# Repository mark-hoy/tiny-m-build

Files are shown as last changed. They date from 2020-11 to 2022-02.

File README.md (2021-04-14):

# tiny-m-build
- [tiny-m-build](#tiny-m-build)
  * [WORK IN PROGRESS](#work-in-progress)
  * [Power](#power)
  * [My BOM](#my-bom)
  * [Build Platform + Plate Information](#build-platform---plate-information)
  * [Stepper Motor Light Reading](#stepper-motor-light-reading)
  * [Frame Assembly](#frame-assembly)
  * [Top](#top)
  * [Hinged TopHat](#hinged-tophat)
- [Electronics](#Electronics)
- [Software](#software)
  * [Raspberry Pi Setup](#raspberry-pi-setup)
  * [Fluidd Pi](#fluidd-pi)
  * [Fluidd](#fluidd)
  * [Mainsail OS](#mainsail-os)
  * [Klipper onto SKR Mini E3 V2](#klipper-onto-skr-mini-e3-v2)
    * [Flashing MCU](#Flashing MCU)
    * [Klipper Configuration](#Klipper Configuration)
  * [Wiring](#wiring)
  
### Klipper Configuration
  
- [Assembly](#assembly)
  * [Rails](#rails)
  * [Rails and Build Plate](#rails-and-build-plate)
- [Extruder](#extruder)
  * [Sherpa Mini](#sherpa-mini)

<small><i><a href='http://ecotrust-canada.github.io/markdown-toc/'>Table of contents generated with markdown-toc</a></i></small>

## WORK IN PROGRESS
This is my particular spin on the Tiny-M build, a variant of the Voron V0 using Mitsumi 2020 Extrusions and Nema 17 motors.  The Voron machines are home build high performance printers. With the V0 being the smallest of the series. The numbering scheme, V0, V1, V2 represent different machines, so don't get confused that's it's a revision.

My version of this is slightly different than the online CAD image. I want to used a BTT SKR mini E3 V2, a 24v heated bed (instead of 120v ac) and a direct drive sherpa mini instead of the regular boden drive.

see the cad image at 
https://github.com/gsl12/Tiny-M

I've finished the build. Will probably go with a simpler enclosure rather than the folding top hat, but need to design it still.
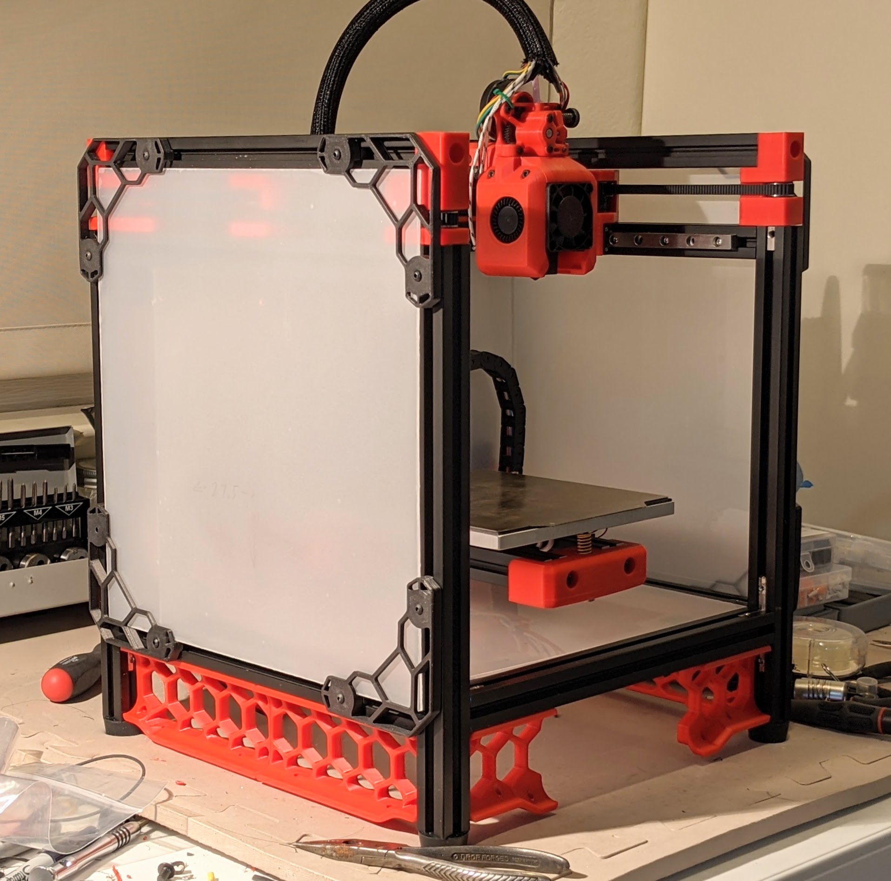
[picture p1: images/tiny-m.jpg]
tiny-m image


Many more build pictures at https://photos.app.goo.gl/qUpFSqQ5FszeDbXW6

The first things I'll link are the Voron V0 build and the Tiny-M repo.
I'd like to use a small direct hot end instead of the standard Voron V0 Boden so that it will easily print flexable material.
In addition, I really like the two position hinged TopHat by hartk1213

There is a very active Discord channel for VoronDesign. The users are really helpful and friendly which for a home build
3d printer is a huge win.

Voron V0 - https://vorondesign.com/voron0

Tiny-M https://github.com/gsl12/Tiny-M

Sherpa Mini-Extruder https://github.com/Annex-Engineering/Sherpa_Mini-Extruder

Hinged Top Hat - https://github.com/gsl12/Tiny-M/tree/master/STLs/usermods/2020_Hinged_TopHat_Print

Motion controller - BIGTREETECH SKR Mini E3 V2.0 New Upgrade Control Board 32Bit with TMC2209 

Job control - Raspberry Pi Zero W, Pi 3 or 4?

T8x4 ptfe coated Lead Screw + POM - 215mm	 *Note: will have to cut to length as this isn't standard.

Many images so far from Xile on Voron group on discord

## Power
Want to use an external 24v supply and then all 24v on the Tiny-M. This means a 24v heated bed which is normally 120v ac. It removed all 120ac from the underside of the build making it a bit safer. Sourcing the bed heater is harder though as is the connection of the power to the chassis.

Got the DC power using the following.

External Mean Well 220 watt 24v DC power supply https://www.digikey.com/en/products/detail/GST220A24-R7B/1866-2085-ND/7703643?itemSeq=348860603 \
Power inlet to match - https://www.digikey.com/en/products/detail/KPJX-PM-4S/2092-KPJX-PM-4S-ND/9990081?itemSeq=348766398 \
Power switch - https://www.digikey.com/en/products/detail/RB141C1000-135/EG5684-ND/8540808?itemSeq=348859736 \
NOTE: The power switch burned it's light out at 24v, suggest adding a voltage drop resistor.

While I really like the idea of 24v of external power with a distribution via this nifty board, I didn't want to have to manufacture a 4 layer board just for my power input, so I decided to go with the simpler solution above....
https://github.com/JNP-1/VoronUsers/tree/master/printer_mods/JNP/PCBs/Supply_PCB

BOM https://github.com/JNP-1/VoronUsers/blob/master/printer_mods/JNP/PCBs/Supply_PCB/BOM/BOM_Supply_PCB_V1.0.txt

Along with an external power brick with a microfit connection\
https://www.digikey.com/en/products/detail/VES220PS24/1470-VES220PS24-ND/10440644?itemSeq=347136397

Use the following when determining how much power a guage of wire can handle https://www.engineeringtoolbox.com/wire-gauges-d_419.html

## My BOM
https://docs.google.com/spreadsheets/d/1UV62ADl2gtK5vL0fV1nwevR6O9Ppzs0MBe7jnsI-jo4/edit?usp=sharing

## Build Platform + Plate Information
The build plate should be either ATP-5 or MIC6 Cast Aluminum 6" x 6" x 1/4" which is about 150mm x 150mm x 6mm onto which a magnetic layer is added, topped with a spring steel build plate.

The heater for the bed should be aprox 0.4 watts/cm^2.  So 15cm x 15cm = 255cm^2    255 * 0.4 = 102 watts. Less power will heat slower, more might be ok, but don't go crazy.  See the following for great info https://duet3d.dozuki.com/Wiki/Choosing_a_bed_heater

## Stepper Motor Light Reading
Many Nema 17 will fit into the space. 
https://duet3d.dozuki.com/Wiki/Choosing_and_connecting_stepper_motors

## Frame Assembly
Depending on if you are drilling + tapping for your rails or using the 90 degree internal connectors (or possibly both!)

If you are drilling (and have a printer) you can make a guide:
See the STL drill template for the holes: 10, 36 and 60

The bottom extrusions have 50mm of space to the bottom of the uprights.
The back is 26mm on the side beams for a total of 26mm + 20mm total (from the back beam).

## Top
While I really like the way the hinged TopHat works, I think I'll go with taller side panels, a taller door panel and a fixed top. I haven't had to have access to the top since I built it. I will re-use the hinged top-hat basic sizes though as the connection into the rails via the M5 is solid.

## Hinged TopHat
The hinged top hat has two positions it can stay in. There is a 2020 TopHat for V0 that I've patterned the following on
(was at https://github.com/gsl12/Tiny-M/tree/master/STLs/usermods/2020_Hinged_TopHat_Print)

**The following measurements have not been verified in an actual build.**\
Verticals\
Back 2 x 75 mm\
Front 2 x 92 mm

Horizontal\
Front 2 x 260 mm\
Back 1 x 260 mm, 1 x 274 mm

Sides\
Top Right/Left 2 x 260 mm\
Bottom Right/Left 2 x 230 mm

Totals\
2 x 75 mm\
2 x 92 mm\
2 x 230 mm\
5 x 260 mm\
1 x 274 mm

# Electronics

The BTT SRK mini E3 V2 (not the older models) is my choice for this build. In pariticular, it has a beefier Mosfet for driving the heater bed. It has many other fine updates too: 2 fan outputs. a proper ground return for drivers, and better thermistor circuitry (thanks Ocho).

Raspberry Pi 3/4, or Zero W.  Any of these will work with Klipper software as it's got a fairly light overhead.

Display - FYSETC V2.1 Mini 12864 is what I have on hand. The wiring to the SRK mini E3 V2 is a bit weird. There is a board that plugs into the USB on the Pi that then easily connects to the two 10 pin connectors. Alternatives are possible here.

For the steppers, I chose all LDO motors which have a great reputation. The X/Y/Z are all 0.9 degree LDO 17HS19-2004S (which also deviates from the original Tiny-M BOM with 1.8 degree steppers).

Endstops - I am using some D2FC-F-7N that I had on hand from fixing a Logitech trackball mouse. (I have to ream out the mounting hole to fit M2). 

I would like to try sensorless homing since the TMC2209 support this mode but have not gotten to this yet.

Additional, stealth chop makes the motors REALLY quiet, this would be pretty cool to also try.

# Software

Thinking of using Raspberry Pi 2 (or 3) with Fluidd and Klipper on BTT SKR Mini E3 V2
By using Fluidd Pi, install should be relatively easy. 

The Raspberry Pi runs Klipper which spits out G-code for the Mini E3 to drive the stepper motors.
The Raspberry Pi connects to the Mini E3 via the USB cable that comes with the Mini E3.

## Raspberry Pi Setup

While I'm using a Pi 4, I'll be trying out FluiddPi, so this is just to get the rest of you going should you want to do it all yourself and download an Image. I strongly suggest you go the FluiddPi route....

Download the latest Raspberry Pi OS Lite image, mine was a 5.4 from Dec 2, 2020 and use Etcher or something similar to burn an SD card with the image. I happened to use a 32G card on a Raspberry Pi 4, but smaller cards and slower Pi will also work.

https://www.raspberrypi.org/software/operating-systems/ \
https://github.com/vladbabii/raspberry_os_buster_read_only_fs

## Fluidd Pi
FluiddPi - A Pi image with Klipper, Moonraker, Fluidd and Web Camera support pre-installed. - cadriel/FluiddPI
https://github.com/cadriel/FluiddPI

1. Download the latest FluiddPi Image, I used v1.2.2 at https://github.com/cadriel/FluiddPI/releases/download/v1.2.2/fluiddpi-rpi-lite-v1.2.2.zip
2. Flash your SD card with the image (fluiddpi-rpi-lite-v1.2.2.zip in my case), I used BalenaEtcher for OSX.
3. Connect the Pi to your monitor (funky adapter cable needed for HDMI on Pi 4) and keyboard, login: pi  password: raspberry
4. Run "sudo raspi-config" and walk through each menu item. \
4a. I choose wireless options and connected to my home wireless, but you could also go wired via Ethernet.\
4b. Give your Pi a hostname and probably set it to your timezone for ease of looking at your log files.\
4c. Enable SSH so that you can remotely get into your Pi\
4d. Update Pi with various patches\
4e. exit 'raspi-config' \
4f. update/upgrade the Linux system "sudo apt update" and "sudo apt upgrade"
4e. Reboot and prove all the stuff you just did works

Run "ifconfig" and determine your IP address. Note: You might want to get the MAC address and set a static IP address in your DCHPD configuration of your Wireless Router. Use SSH (on OSX/Linux) or PuTTY on Windows and remotely login to your Pi. The command will be similar to "ssh pi@192.168.1.164" but with your IP address.

In addition, if you browse on your network to http://192.168.1.164/fluidd#/configuration you can start configuration of your system

## Fluidd
https://github.com/cadriel/fluidd/blob/develop/docs/README.md

## Mainsail OS
https://github.com/raymondh2/MainsailOS/releases

How to install \
https://www.youtube.com/watch?v=MK0-MDVJG94

How to configure mainsail \
https://meteyou.github.io/mainsail/setup/

Connecting \
https://discord.com/channels/460117602945990666/741806179247980695/768032201362767893

Web Camera for Mainsail https://lazarofilm.gitbook.io/3d-printing/setting-up-your-pi-camera-for-mainsail

## Klipper onto SKR Mini E3 V2

Klipper code needs to run on the Pi and communicate with the MCU. Our MCU is the BTT SKR Mini E3 V2 and the following is how to set it up.

Note pin difference from earlier SKR mini boards. \

https://github.com/VoronDesign/Voron-0/pull/51 for V2 vs V1.x difference \
https://discord.com/channels/460117602945990666/696930677161197640/746051951447375983 \
https://github.com/VoronDesign/Voron-0/blob/master/VORON-0/Manuals/V0_Setup_Guide.pdf

Another example configuration of SKR Mini E3 V2 for klipper \
https://github.com/KevinOConnor/klipper/blob/master/config/generic-bigtreetech-skr-mini-e3-v2.0.cfg

Copy the appropriate file from the configuration directory in this github to /home/pi/klipper_config/printer.cfg (or similar if you have it in a different place.

Example: OSX & Linux
```console
$ scp configuration/printer.skr.mini.e3.v2.cfg pi@192.168.1.164:/home/pi/klipper_config/printer.cfg
```

Use the following as a reference for configuration of Klipper for BTT SKR mini E3 V2 \
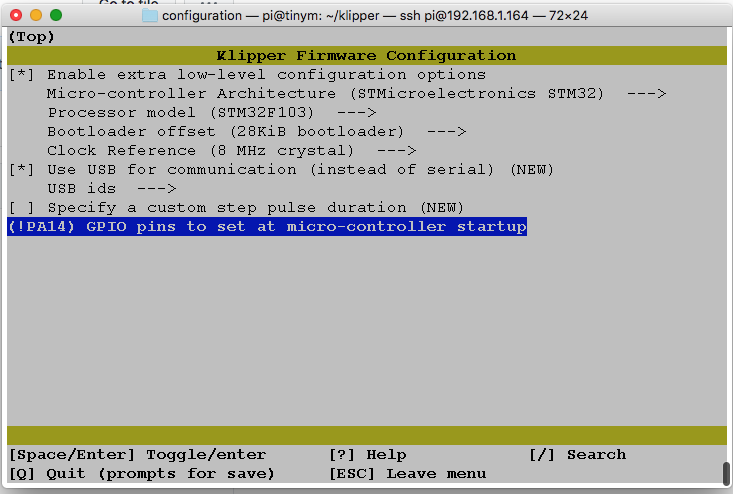
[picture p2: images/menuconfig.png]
cfg image


Then, on the Pi move to the klipper directory
```console
$ cd klipper
$ make menuconfig
. 
. 
. 
~/klipper $ cp out/klipper.bin ~/firmware.bin
```

### Flashing MCU

1. Now remove the SD card from the SKR mini and copy this file onto it.
2. Place card into MCU and apply 24v power, wait 1 minute and turn power off
3. Remove card, and look at the contents and the "firmware.bin" file should have been renamed to "FIRMWARE.CUR" 
4. The MCU is now up to date and ready to work with Klipper

### Klipper Configuration

First power on the Pi and then the SKR Mini E3 V2 then log into the Pi and run a couple of commands

Issue the following command, then plug in the USB cable and you should see something like:

```console
$ dmesg -w -t
...
cdc_acm 1-1.1:1.0: ttyACM0: USB ACM device 
usb 1-1.1: USB disconnect, device number 5 
usb 1-1.1: new full-speed USB device number 6 using xhci_hcd 
usb 1-1.1: New USB device found, idVendor=1d50, idProduct=614e, bcdDevice= 1.00 
usb 1-1.1: New USB device strings: Mfr=1, Product=2, SerialNumber=3 
usb 1-1.1: Product: stm32f103xe 
usb 1-1.1: Manufacturer: Klipper 
usb 1-1.1: SerialNumber: 35FFDB054246313020791057 
cdc_acm 1-1.1:1.0: ttyACM0: USB ACM device
```

Klipper should now be able to use a mapping that contains the serial number, copy this info into the 'serial' line in the configuration file

```console
$ ls /dev/serial/by-id/
usb-Klipper_stm32f103xe_35FFDB054246313020791057-if00
```

Edit the klipper_config file
```console
$ vi klipper_config/printer.cfg 
```

So now the cfg should contain your printer
```console
$ grep serial klipper_config/printer.cfg 
serial: /dev/serial/by-id/usb-Klipper_stm32f103xe_35FFDB054246313020791057-if00
```

If you don't see the /dev/by/serial section, double check your USB cable and ensure each board is correctly powered on.

For Klipper to run without throwing errors, it expects to see valid information from it's configured thermistors. So wire up the hotend thermistor to PA0.

If you don't have a heated bed (or it's not installed yet), then comment out the "[heater_bed]" section as well as the last 5 lines of the printer.cfg file

Remove the last 5 lines in printer.cfg file\
#*# [heater_bed]\
#*# control = pid\
#*# pid_kp = 37.593\
#*# pid_ki = 1.139\
#*# pid_kd = 310.142\

## Wiring Guide
Follow the V0 guide for steppers, limit switches, hot end, bed heater, bed thermal cutoff switch, etc.

The best set of info for this is the V0 assembly manual which is oddly not on the Voron main site, but only in the GitHub location
https://github.com/VoronDesign/Voron-0/blob/master/VORON-0/Manuals/V0_Setup_Guide.pdf

The Wago wire connectors can make your life a bit easier too.

Basic stepper setup
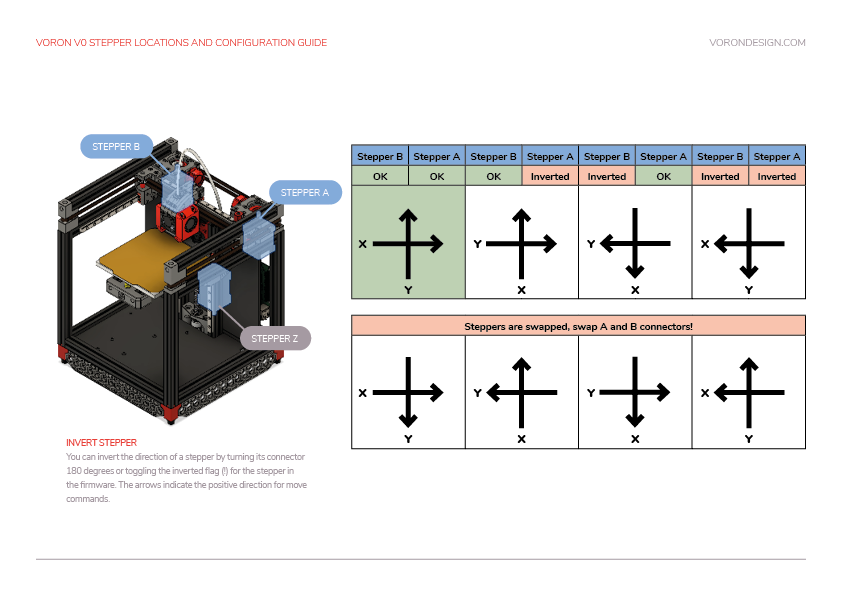
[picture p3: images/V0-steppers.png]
cfg image


Back Left Motor B Connects to X\
Back Right Motor A Connects to Y

Direction of X is inverted as well as Y in the configuration file (at least for my wiring).

# Assembly 

## Rails
Watch the video and note that if you use the 90 degree internal corners, you'll only need two holes in the build plate. You'll still have a bunch of tapping though so worth watching. \
https://www.youtube.com/watch?v=2dvbn0rWA60&feature=youtu.be

## Rails and Build Plate
Carefully review the Tiny-M CAD via OnShape 
https://github.com/gsl12/Tiny-M \
While I found OnShape slow to load on my aging 2011 iMac, it did pretty darn good once loaded.

I believe (but have not verified) that assembly of the tiny-m should be very similar to the V0 rails and build plate, so watch the following video:\
https://youtu.be/Il6koDFPf7w

Build Plate - Wago 221 connectors make for very nice connections on the printer. They are not rated for the temperature at the bed, but unless you are running a very hot enclosed build, they should be OK a distance away. I used a couple of these holders mounted to the rails under the build plate. https://www.thingiverse.com/thing:4579456 The Wago 221 snap into place very firmly.

# Extruder

## Sherpa Mini 
From Anin at https://discord.com/channels/641407187004030997/705183604535459871/785714455178248192

Coffee's video shows the correct assembly order for a K series printer where the lower two screws thread into the toolhead. For a standalone sherpa it might be easier to assemble things in this order:\
1. Install all inserts (including 2 in the rear housing) and bearings, clean up the filament path with a 2mm drill bit\
2. Sand/grind shaft (use the printed tool if necessary)\
3. Insert the 50t gear/shaft assy into the bearing\
4. Stack the core housing on top of the rear housing and install the lower two screws\
5. Install the driven BMG filament gear, add a 5x7x0.5mm waher on top of the gear. Loctite the grub screw\
6. Build and install the idler arm assembly\
7. Install the front housing\
8. Make sure everything runs freely\
9. Install the motor and adjust gear meshing until there is only a tiny bit of backlash\
10. Install the tensioner screw assembly\
Note also that the tensioner screw insert can be up to 6mm long

The video reference.\
https://youtu.be/3WogD5IUwAM
https://www.youtube.com/watch?v=3WogD5IUwAM&t=6s

Images of Dragon for Sherpa Mini \
https://github.com/Annex-Engineering/Sherpa_Mini-Extruder/tree/master/Toolheads/Xile_Tiny_M/Dragon%20Toolhead/Images

Wiring: With the LDO pancake motor I did the wiring as follows: Blue-Yellow-Green-Red

**NOTE: There is a small 37mm (or so) boden tube between the Sherpa Mini and the Extruder. On the end that goes into the Sherpa Mini, enlarge the end with a drill bit so that filament feeds do not get stuck. **

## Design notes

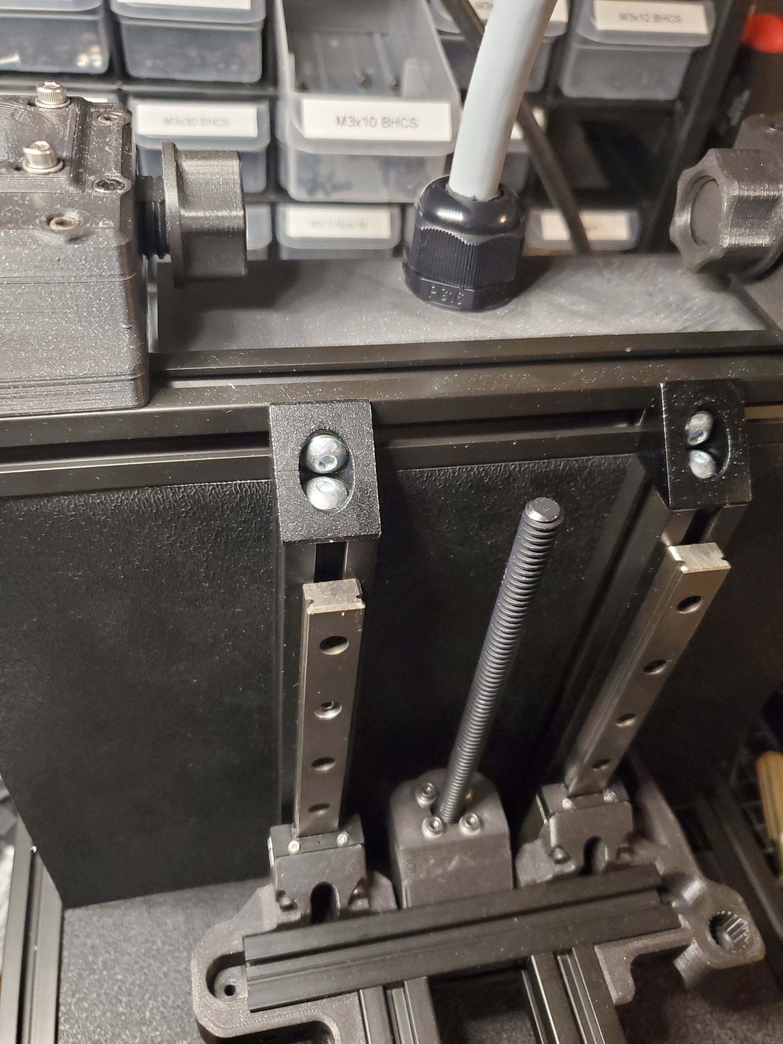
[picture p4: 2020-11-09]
images/connector90degree.jpg

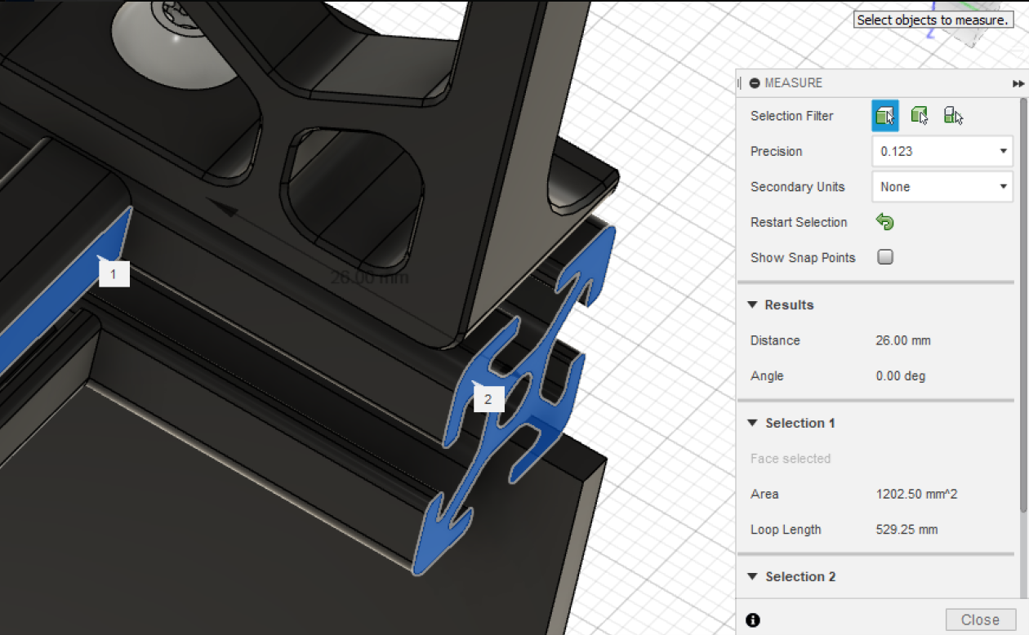
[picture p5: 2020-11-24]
images/edge-spacing.png

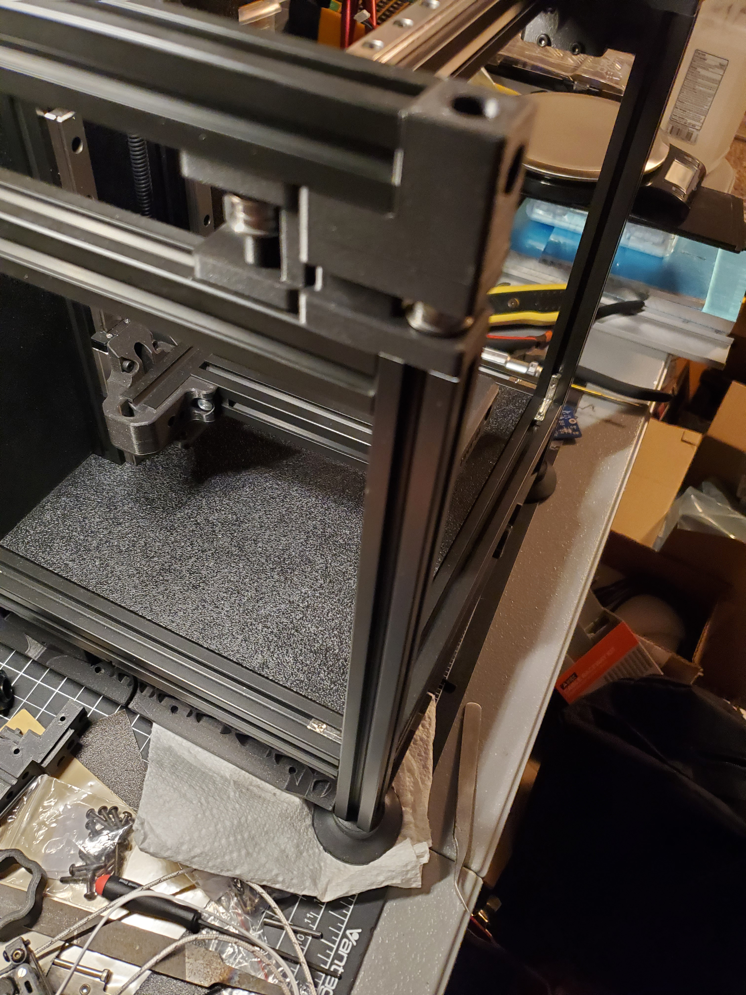
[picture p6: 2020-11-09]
images/left-side2.jpg

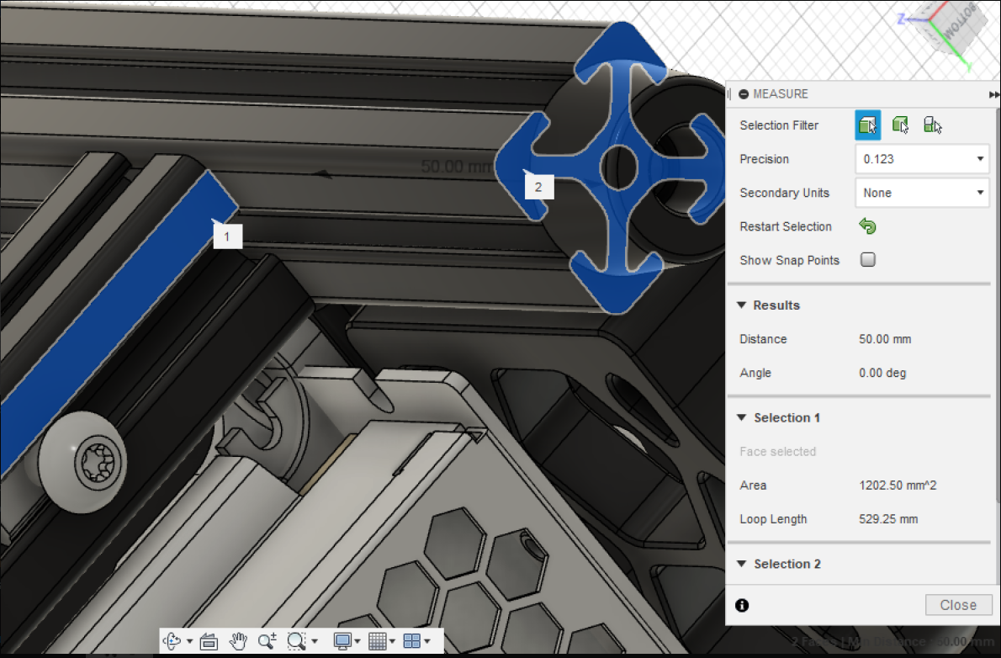
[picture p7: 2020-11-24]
images/bottom-spacing.png

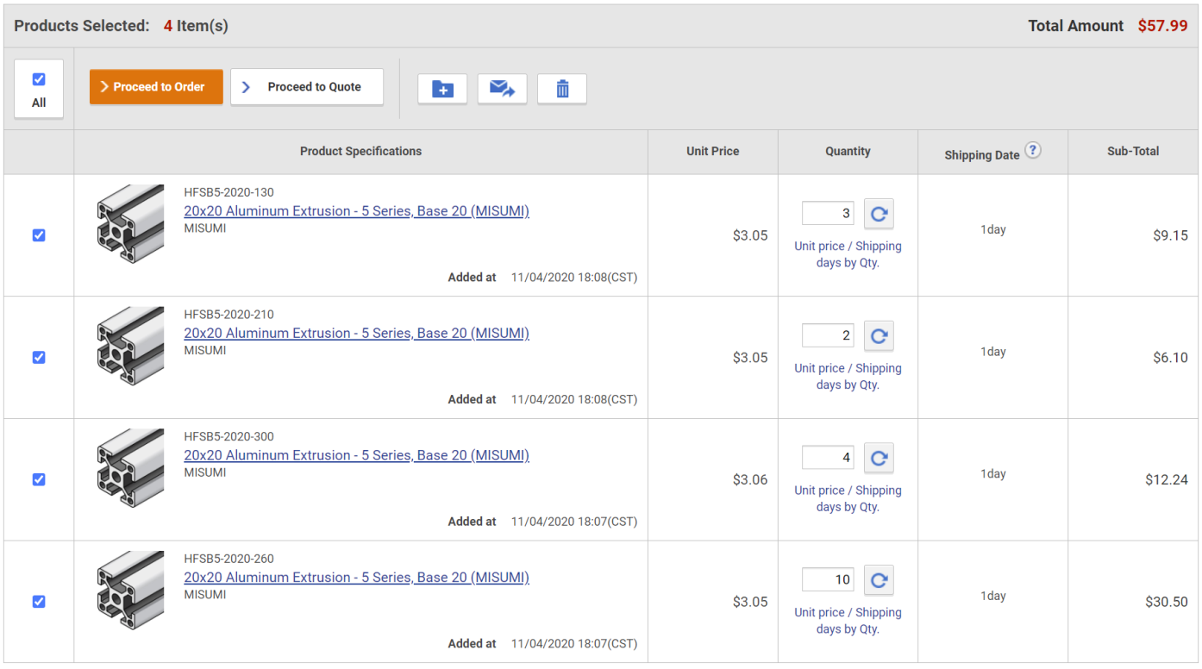
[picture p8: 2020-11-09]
images/misumi-frame.png

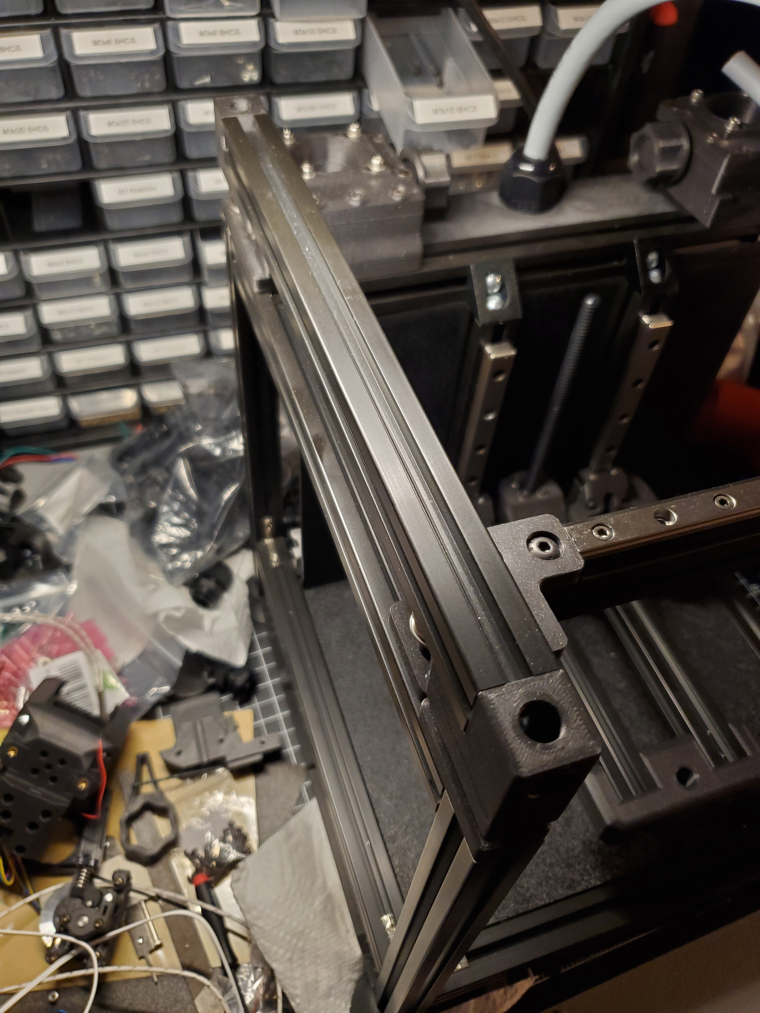
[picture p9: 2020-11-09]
images/left-side.jpg

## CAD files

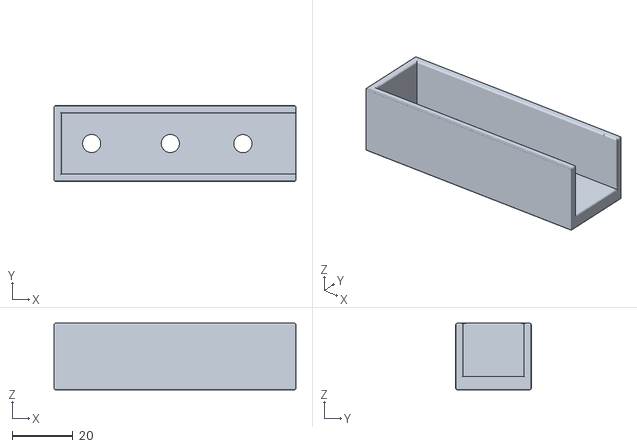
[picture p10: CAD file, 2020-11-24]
Tiny-M_Frame_Guide.stl
80.0 x 25.0 x 22.0

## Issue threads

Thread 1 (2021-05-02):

External PSU wiring?

simplisticton, 2021-05-02:
Can you provide a wiring diagram for how you wired up the PSU & the switch? I'm planning a V0 build and want to do the same as you did with the external 24V PSU.

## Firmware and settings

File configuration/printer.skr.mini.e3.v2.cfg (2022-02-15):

# This file contains common pin mappings for the BIGTREETECH SKR mini
# E3 v2.0. To use this config, the firmware should be compiled for the
# STM32F103 with a "28KiB bootloader". Also, select "Enable extra
# low-level configuration options" and configure "GPIO pins to set at
# micro-controller startup" to "!PA14".

# The "make flash" command does not work on the SKR mini E3. Instead,
# after running "make", copy the generated "out/klipper.bin" file to a
# file named "firmware.bin" on an SD card and then restart the SKR
# mini E3 with that SD card.

# See docs/Config_Reference.md for a description of parameters.

# See the example.cfg file for a description of available parameters.

# Back Left Motor B Connects to X on SKR mini E3 V2
# Back Right Motor A Connects to Y
#
# Stepper X and Y are inverted directions (at least for my wiring)

# Moving Gantry is the X limit switch
# Switch on the Motor A mount is the Y limit switch
# Switch on the Z platform is the Z limit switch

[mcu]
serial: /dev/serial/by-id/usb-Klipper_stm32f103xe_30FFDC055346323034740743-if00

[display]
#    FYSETC mini12864 LCD Display v2.1
lcd_type: uc1701
cs_pin: PB8
a0_pin: PB15
rst_pin: PB9
encoder_pins: ^PA9,^PA10
click_pin: ^!PB5
contrast: 63
spi_software_sclk_pin: PA5
spi_software_mosi_pin: PA7
spi_software_miso_pin: PA6

[neopixel fysetc_mini12864]
#    To control Neopixel RGB in mini12864 display
pin: PA15
chain_count: 3
initial_RED: 1.0
initial_GREEN: 0.0
initial_BLUE: 0.0
color_order: RGB

[stepper_x]
step_pin: PB13
dir_pin: !PB12
enable_pin: !PB14
step_distance: .00625
endstop_pin: PC0 
position_endstop: 153
position_max: 154
position_min: -3
homing_speed: 5   #Max 100, suggest 50 once configuration of motors and home is correct
homing_retract_dist: 5
homing_positive_dir: true

[tmc2209 stepper_x]
uart_pin: PC11
tx_pin: PC10
uart_address: 0
microsteps: 16
run_current: 1.0
hold_current: 0.500
stealthchop_threshold: 1

[stepper_y]
step_pin: PB10
dir_pin: !PB2
enable_pin: !PB11
step_distance: .00625
endstop_pin: PC1
position_endstop: 152.5
position_max: 152.5
position_min:-3
homing_speed: 5   #Max 100, suggest 50 once configuration of motors and home is correct
homing_retract_dist: 5
homing_positive_dir: true

[tmc2209 stepper_y]
uart_pin: PC11
tx_pin: PC10
uart_address: 2
microsteps: 16
run_current: 1.0
hold_current: 0.500
stealthchop_threshold: 1

[stepper_z]
step_pin: PB0
dir_pin: PC5
enable_pin: !PB1
step_distance: 0.0006250 #for T8x4 lead screw
endstop_pin: PC2
position_endstop: .650
position_max: 150
position_min: -1
homing_speed: 5   #Max 100, suggest 10 once configuration of motors and home is correct
second_homing_speed: 3.0
homing_retract_dist: 3.0

[tmc2209 stepper_z]
uart_pin: PC11
tx_pin: PC10
uart_address: 1
microsteps: 16
run_current: 1.0
hold_current: 0.500
stealthchop_threshold: 5


[extruder]
step_pin: PB3
dir_pin: !PB4
enable_pin: !PD2
step_distance: 0.001423 #calibrate this value for your individual printer!!
nozzle_diameter: 0.400
filament_diameter: 1.750
heater_pin: PC8
sensor_type: EPCOS 100K B57560G104F
sensor_pin: PA0
#control: pid
#pid_Kp: 22.2
#pid_Ki: 1.08
#pid_Kd: 114
min_temp: 0
max_temp: 270
min_extrude_temp: 170
max_extrude_only_distance: 780.0
max_extrude_cross_section: .8
Pressure_advance: 0.0
pressure_advance_smooth_time: 0.040

[tmc2209 extruder]
uart_pin: PC11
tx_pin: PC10
uart_address: 3
microsteps: 16
run_current: 0.300
hold_current: 0.250
stealthchop_threshold: 5

[heater_bed]
heater_pin: PC9
sensor_type: NTC 100K beta 3950
#sensor_type: NTC 100K MGB18-104F39050L32
sensor_pin: PC3
smooth_time: 3.0
max_power: 0.6
#control: pid
min_temp: 0
max_temp: 120
#pid_kp: 58.437
#pid_ki: 2.347
#pid_kd: 363.769

[printer]
kinematics: corexy
max_velocity: 250
max_accel: 2000
max_z_velocity: 10
max_z_accel: 30
square_corner_velocity: 5.0

[heater_fan hotend_fan]
# Hotend Fan
pin: PC7
max_power: 1.0
kick_start_time: 0.5
heater: extruder
heater_temp: 50.0
#If you are experiencing back flow, you can reduce fan_speed
#fan_speed: 1.0

[fan]
# Print Cooling Fan - XYE board, Fan Pin
pin: PC6
kick_start_time: 0.5
#depending on your fan, you may need to increase or reduce this value
#if your fan will not start
off_below: 0.13
cycle_time: 0.010

[idle_timeout]
timeout: 180000


[homing_override]
axes: xyz
set_position_z: 0
gcode:
   G90
   G0 Z5 F600
   G28 X Y
   G0 X153 Y132 F3600 
   
   G28 Z
   G0 Z10 F1800
   G0 X60 Y60 Z20 F3600

   # Tool to help adjust bed leveling screws. One may define a
# [bed_screws] config section to enable a BED_SCREWS_ADJUST g-code
# command.
[bed_screws]
screw1: 60,5
screw1_name: front screw
screw2: 5,115
screw2_name: back left
screw3: 115,115
screw3_name: back right

[virtual_sdcard]
path: ~/uploads/

[pause_resume]

[display_status]

[gcode_macro CANCEL_PRINT]
rename_existing: BASE_CANCEL_PRINT
gcode:
    TURN_OFF_HEATERS
    CLEAR_PAUSE
    SDCARD_RESET_FILE
    BASE_CANCEL_PRINT

[gcode_macro PRINT_START]
#   Use PRINT_START for the slicer starting script - please customise for your slicer of choice
gcode:
    G28                            ; home all axes
    G1 Z20 F3000                   ; move nozzle away from bed
   
[gcode_macro PRINT_END]
#   Use PRINT_END for the slicer ending script - please customise for your slicer of choice
gcode:

    M400                           ; wait for buffer to clear
    G92 E0                         ; zero the extruder
    G1 E-4.0 F3600                 ; retract filament
    G91                            ; relative positioning

    #   Get Boundaries
    {% set max_x = printer.configfile.config["stepper_x"]["position_max"]|float %}
    {% set max_y = printer.configfile.config["stepper_y"]["position_max"]|float %}
    {% set max_z = printer.configfile.config["stepper_z"]["position_max"]|float %}

    #   Check end position to determine safe direction to move
    {% if printer.toolhead.position.x < (max_x - 20) %}
        {% set x_safe = 20.0 %}
    {% else %}
        {% set x_safe = -20.0 %}
    {% endif %}

    {% if printer.toolhead.position.y < (max_y - 20) %}
        {% set y_safe = 20.0 %}
    {% else %}
        {% set y_safe = -20.0 %}
    {% endif %}

    {% if printer.toolhead.position.z < (max_z - 2) %}
        {% set z_safe = 2.0 %}
    {% else %}
        {% set z_safe = max_z - printer.toolhead.position.z %}
    {% endif %}

    G0 Z{z_safe} F3600    ; move nozzle up
    G0 X{x_safe} Y{y_safe} F20000    ; move nozzle to remove stringing
    TURN_OFF_HEATERS
    M107                           ; turn off fan
    G90                            ; absolute positioning
    G0 X60 Y{max_y} F3600          ; park nozzle at rear
	
[gcode_macro LOAD_FILAMENT]
gcode:
   M83                            ; set extruder to relative
   G1 E280 F1800                  ; quickly load filament to down bowden
   G1 E30 F300                    ; slower extrusion for hotend path
   G1 E15 F150                    ; prime nozzle with filament
   M82                            ; set extruder to absolute
    
[gcode_macro UNLOAD_FILAMENT]
gcode:
   M83                            ; set extruder to relative
   G1 E10 F300                    ; extrude a little to soften tip
   G1 E-380 F1800                 ; retract filament completely
   M82                            ; set extruder to absolute
   
   
[gcode_macro PAUSE]
rename_existing: BASE_PAUSE
default_parameter_X: 230    # edit to your preferred park position
default_parameter_Y: 230    # edit to your preferred park position
default_parameter_Z: 10     # edit to your preferred park position
default_parameter_E: 1      # edit to your preferred retract length
gcode:
    SAVE_GCODE_STATE NAME=PAUSE_state
    BASE_PAUSE
    G91
    G1 E-{E} F2100
    G1 Z{Z}
    G90
    G1 X{X} Y{Y} F6000
    
[gcode_macro RESUME]
rename_existing: BASE_RESUME
default_parameter_E: 1      # edit to your preferred retract length
gcode:
    G91
    G1 E{E} F2100
    G90
    RESTORE_GCODE_STATE NAME=PAUSE_state MOVE=1
    BASE_RESUME

# Sensor Types
#   "EPCOS 100K B57560G104F"
#   "ATC Semitec 104GT-2"
#   "NTC 100K beta 3950"
#   "Honeywell 100K 135-104LAG-J01"
#   "NTC 100K MGB18-104F39050L32" (Keenovo Heater Pad)
#   "AD595"
#   "PT100 INA826"

#*# <---------------------- SAVE_CONFIG ---------------------->
#*# DO NOT EDIT THIS BLOCK OR BELOW. The contents are auto-generated.
#*#
#*# [extruder]
#*# control = pid
#*# pid_kp = 22.376
#*# pid_ki = 0.994
#*# pid_kd = 125.866
#*#
#*# [heater_bed]
#*# control = pid
#*# pid_kp = 37.593
#*# pid_ki = 1.139
#*# pid_kd = 310.142

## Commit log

2020-11-08 Update README.md
    Added link to hinged top hat
2020-11-09 Update README.md
    added leadscrew info
2020-11-21 Update README.md
    Added BOM and WORK IN PROGRESS
2020-11-21 Update README.md
    Added info on build platform/plate and stepper
2020-11-24 Update README.md
    Started to add info on frame drilling/assembly
2020-11-24 Drilling guide
    [Tiny-M_Frame_Guide.stl]
2020-11-25 Add files via upload
    Blind holes in back of Z support from Xile
2020-11-29 Update README.md
    Added info on MainsailOS and Hinged TopHat 2020
2020-11-29 Update README.md
    Preliminary sizes of hinged top hat Mitsumi 2020
2020-11-30 Update README.md
    Added configuration for klipper on SKR
2020-11-30 Update README.md
    Updated Hinged TopHat for Tiny-M width/depth vs V0
2020-12-04 Update README.md
    LInk to LCD wiring in discord
2020-12-04 Add files via upload
    Image from discord on LCD wiring
2020-12-07 Update README.md
    Added info on Pi to use 2/3 vs 3/4 and Fluid Pi to do the install of Klipper, Moonraker, Fluidd and with camera support
    Links to various topics for setup
2020-12-08 Added info on Mini Sherpa assembly
2020-12-08 Added web camera setup link for mainsail
2020-12-08 Added a Rails and Build plate section
    Added Tiny-M from Onshape and link to V0 assembly of rails and build plate
    Added start of extruder section
2020-12-08 Added link to Nero 3DP joint assembly
2020-12-11 Update README.md
    Added info on 24v external power
2020-12-14 moved sherpa mini to under extruder
2020-12-16 updates on 24v heater bed
2020-12-22 updated power section
2020-12-22 added configuration file for SKR mini E3 V2
    [printer.skr.mini.e3.v2.cfg]
2020-12-23 updated header info in cfg file
    [printer.skr.mini.e3.v2.cfg]
2020-12-23 preliminary klipper setup
2020-12-23 added flashing MCU with klipper
2020-12-23 added usb cfg into klipper printer.cfg file
2020-12-23 Kllipper cfg for PA0
    Also commented on removing [heater_bed] if you don't have a thermistor for it.
2020-12-23 clear image of steppers from V0 manual
2020-12-23 Added a quick wiring guide
    Used the V0 wiring guild that Xile pointed out
2020-12-25 add X/Y motor A/B info
2020-12-25 set default homing speeds to 5 for beginners
    [printer.skr.mini.e3.v2.cfg]
2020-12-25 added motor and limit switch info
    [printer.skr.mini.e3.v2.cfg]
2020-12-25 changed hold_currents on xyz to 0.3 instead of 0.5
    [printer.skr.mini.e3.v2.cfg]
2020-12-26 Added 37mm boden between toolhead and extruder
2020-12-27 added LDO pancake motor wiring colors
    Once again thanks to Xile for the correct color combo
2021-01-09 Added link to Wago 221 mount
2021-01-09 Hinged Top Hat link in Tiny-M github repo now.
2021-01-13 Added current picture
2022-02-15 Update printer.skr.mini.e3.v2.cfg
    Add in FYSETC mini12864 display settings
    [printer.skr.mini.e3.v2.cfg]
2022-02-15 Update printer.skr.mini.e3.v2.cfg
    Set X and Y stealthchop_threshold to 1 for now. Investigate spreadCycle for future use
    Set X/Y/Z hold current to .500
    [printer.skr.mini.e3.v2.cfg]
